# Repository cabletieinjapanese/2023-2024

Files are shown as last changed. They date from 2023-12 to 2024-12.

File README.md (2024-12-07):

repository for robocup bot, 2024 Singapore Robocup Open season

*updated 5 apr 2024*
## team, roles
loh hao yuan - elec, programming

lee yu zhe - mech, programming

cruz low, oliver ong - logistics, soldering

## final results
(5 apr 2024) 
due to a variety of factors (including misinterpretation of registration information, delays in robot production, lack of time for organiser to make adjustments), we were unable to participate in the 2024 Singapore Robocup Open.

throughout the past year, we've learnt a lot about the workings of a robocup bot, and we'll be back next year to finally prove our worth

we're currently working to finish up and polish our bot, such that we can run a few scrim games before starting anew with our bot for the 2024-2025 season.

## remarks
* everything here is half cooked spaghetti
    * we spent a lot of our time this year trying to figure things out, so a lot of stuff here is the result of trial and error
    * i guess our learning can be shown through the different versions, but theres many many areas which have a lot of potential for improvement
* version control
    * we didn't really use our github repository that much, which is a really bad practice
    * furthermore, one of our members has still not figured out how version control works, and consistently asks me to "help (him) push the code"  

## thanks
* [Sentinels Robotics](https://github.com/senrobo)
    * [@vincentcayadi](https://github.com/vincentcayadi) for his advice regarding the sport and life as a whole, his boundless enthusiasm, faith in our capabilities and good humour
    * [@shuanluck](https://github.com/shuanluck), [@DavidLow22](https://github.com/DavidLow22), and Tan Kian Wu for advice in all areas of robocup
* [Ducc Robotics](https://github.com/8076ducc)
    * [@neohaojun](https://github.com/neohaojun) for guidance and advice with regards to budgeting

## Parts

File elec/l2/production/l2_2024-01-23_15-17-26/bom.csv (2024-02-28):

Designator | Footprint | Quantity | Value | LCSC Part #
AWG1, AWG2 | 14 AWG | 2 | MountingHole
C1 | cap0603 | 1 | 10n
C2, C5 | EIA-7343-D | 2 | 220u
C3, C6 | cap0603 | 2 | C
C4 | cap0603 | 1 | 10u
D1_2, D1 | DIOM7959X265N | 2 | B340
H10, H11, H12, H13, H14, H3, H4, H5, H6, H7, H8, H9 | MountingHole_3.2mm_M3_Pad_Via | 12 | MountingHole_Pad
J1, J2 | L298N | 2 | Conn_01x06
J3 | PinSocket_1x04_P1.27mm_Vertical | 1 | Conn_01x04
J5 | PinSocket_1x08_P2.54mm_Vertical | 1 | Conn_01x08
L1, L2 | 0630 One Piece Inductor | 2 | 15uH
R1, R101, R3 | res0603 | 3 | 10K
R102 | res0603 | 1 | 1K
R2 | res0603 | 1 | 5K9
R4 | res0603 | 1 | 3K24
SW101 | SW_PUSH_SPST | 1 | SW_Push
U1, U3 | TI_SO-PowerPAD-8 | 2 | TPS5430DDA
U2 | MODULE_DEV-15583 | 1 | DEV-15583

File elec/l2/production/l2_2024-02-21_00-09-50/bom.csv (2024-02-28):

Designator | Footprint | Quantity | Value | LCSC Part #
C1 | cap0603 | 1 | 10n
C2, C5 | EIA-7343-D | 2 | 220u
C3, C6 | cap0603 | 2 | C
C4 | cap0603 | 1 | 10u
D1, D2 | 0603 | 2 | B340
H1, H10, H11, H12, H13, H14, H15, H16, H2, H3, H4, H5, H6, H7, H8, H9 | MountingHole_3.2mm_M3_Pad_Via | 16 | MountingHole_Pad
J1, J2 | L298N | 2 | Conn_01x13
J3 | PinHeader_1x04_P2.54mm_Vertical | 1 | Conn_01x04
J5 | PinSocket_1x08_P2.54mm_Vertical | 1 | Conn_01x08
L1, L2 | 0630 One Piece Inductor | 2 | 15uH
R1, R101, R3 | res0603 | 3 | 10K
R102 | res0603 | 1 | 1K
R2 | res0603 | 1 | 5K9
R4 | res0603 | 1 | 3K24
SW101 | SW_PUSH_SPST | 1 | SW_Push
U1, U3 | TI_SO-PowerPAD-8 | 2 | TPS5430DDA
U2 | MODULE_DEV-15583 | 1 | DEV-15583
batawg1, batawg2 | 14 AWG | 2 | +12V

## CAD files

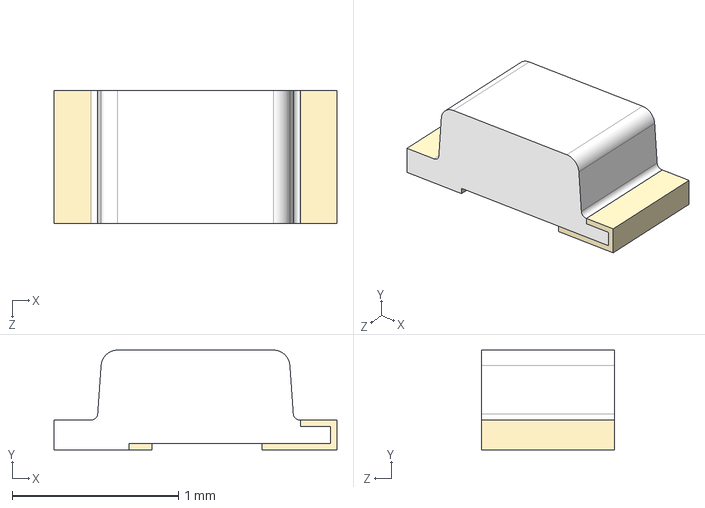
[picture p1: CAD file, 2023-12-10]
elec/2024l1/3dmodels/ALS-PT19.step
1.70 x 0.6 x 0.8 mm

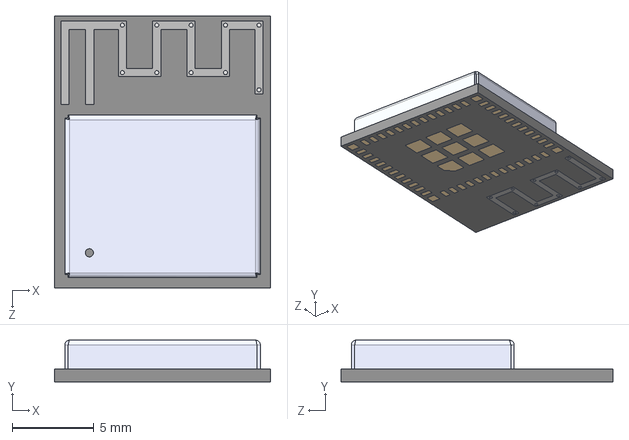
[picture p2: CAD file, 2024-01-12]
elec/l2/ESP32-C/ESP32-C3-MINI-1-N4.step
13.2 x 2.55 x 16.6 mm

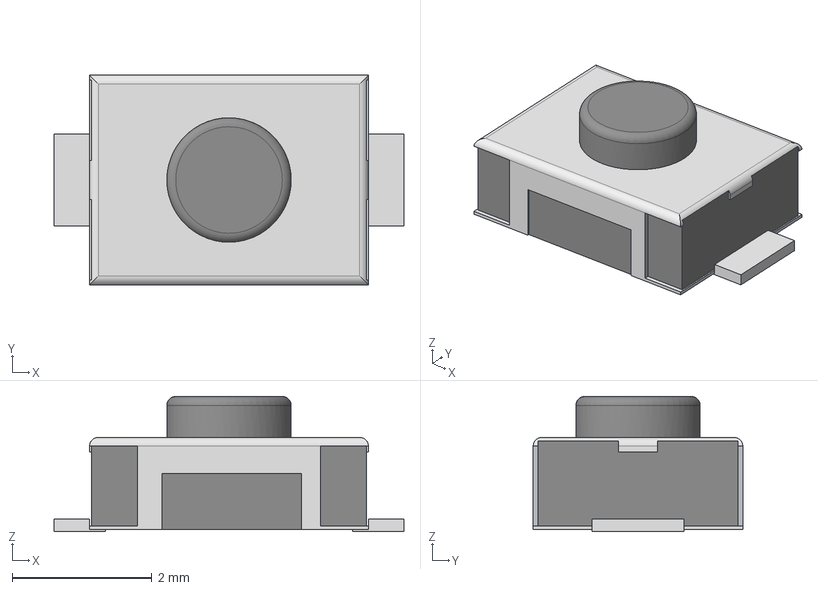
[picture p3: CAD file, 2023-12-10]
elec/2024l1/3dmodels/SW_PUSH_SPST.step
5.00 x 3.00 x 1.93 mm

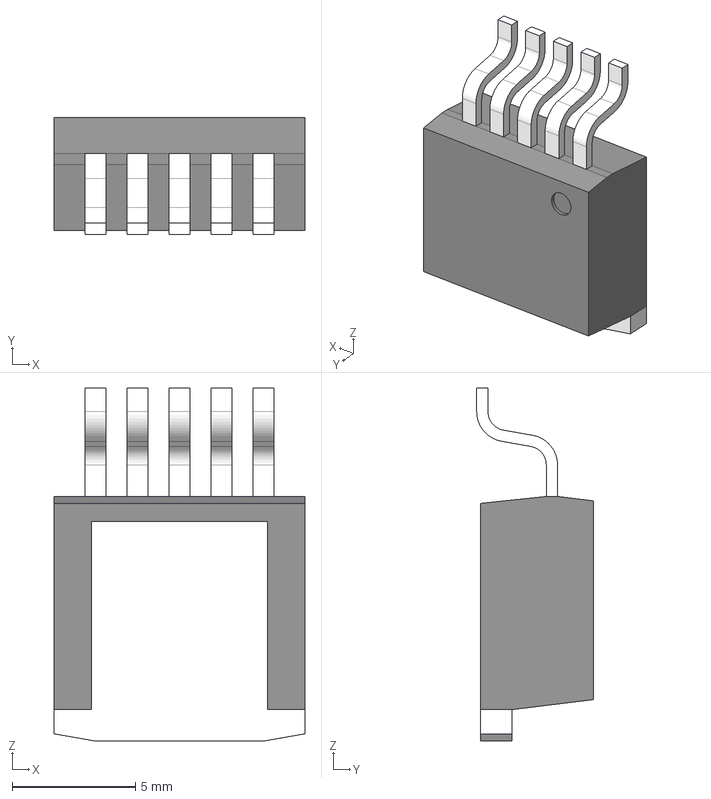
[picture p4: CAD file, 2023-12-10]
elec/2024l1/3dmodels/LM2587S.stp
10.2 x 4.72 x 14.3 mm
BODY_TS5B
HTSINK_TS5B
LEAD_TS5B x 5

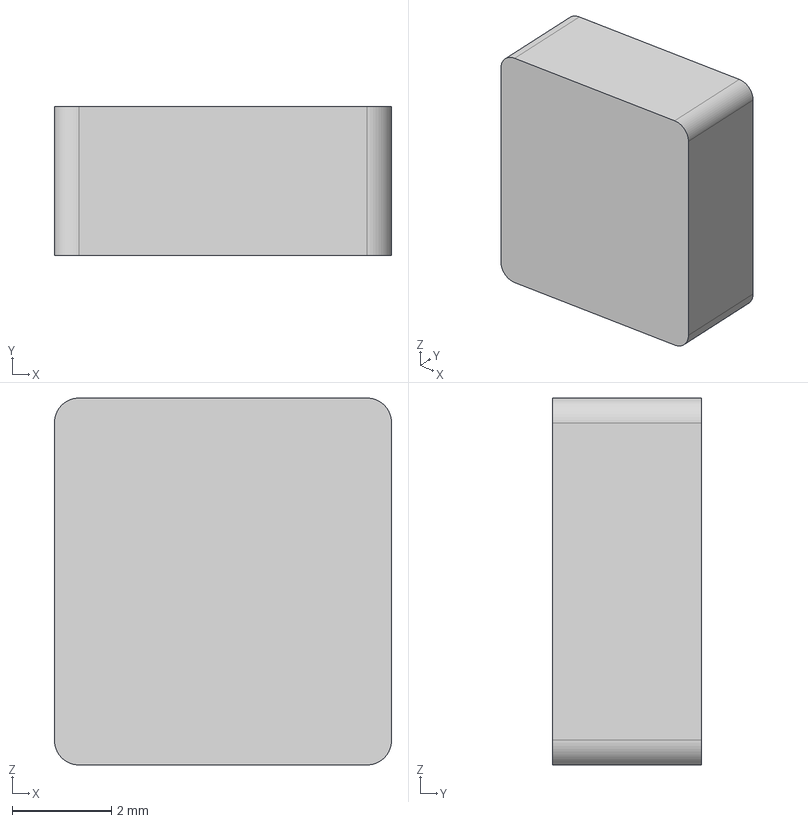
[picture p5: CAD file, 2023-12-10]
elec/2024l1/3dmodels/0603Inductor.step
6.80 x 3.00 x 7.40 mm

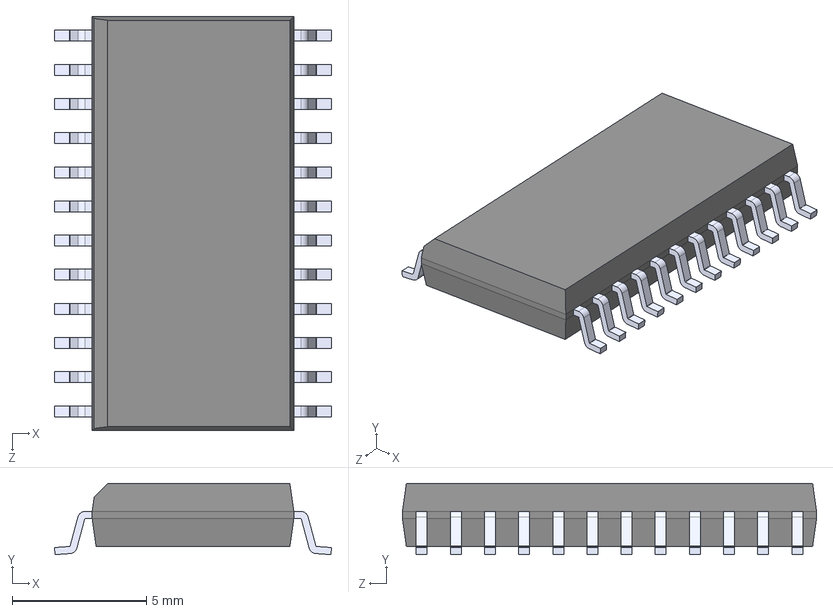
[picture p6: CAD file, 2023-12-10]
elec/2024l1/3dmodels/CD74HC4067M.step
10.3 x 2.65 x 15.4 mm

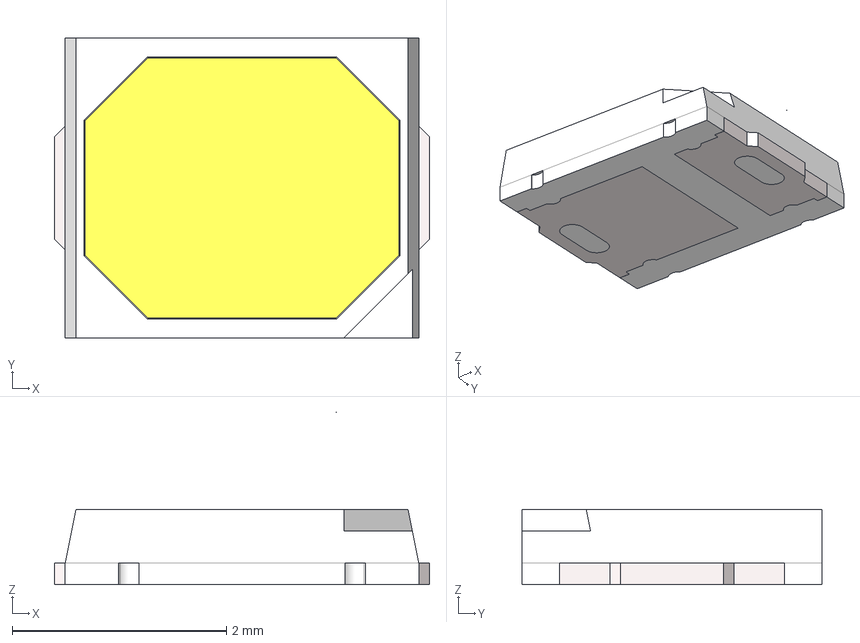
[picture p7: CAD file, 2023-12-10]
elec/2024l1/3dmodels/led2835.stp
3.50 x 2.80 x 1.61 mm

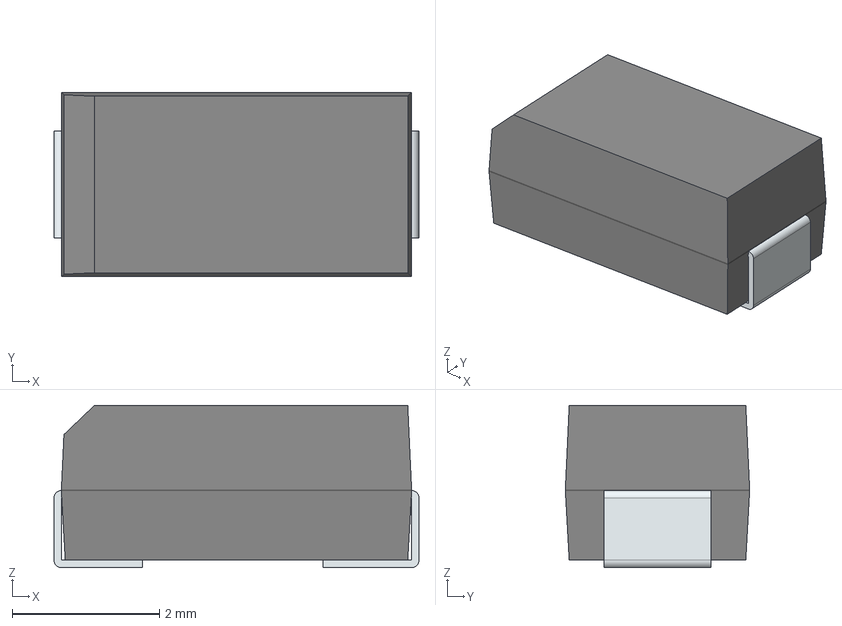
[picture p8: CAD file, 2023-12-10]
elec/2024l1/3dmodels/SS5X.stp
4.95 x 2.50 x 2.20 mm
FilletPin1
FilletPin2

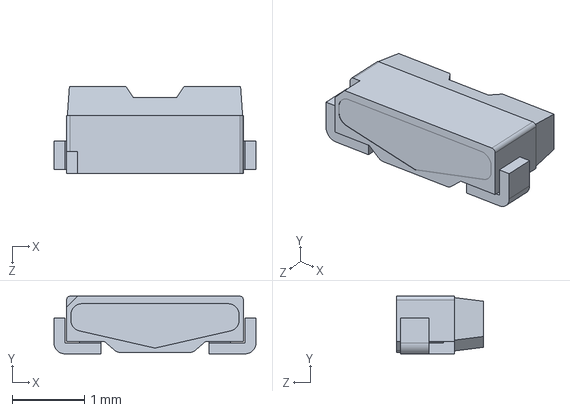
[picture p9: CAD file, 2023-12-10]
elec/2024l1/3dmodels/CSL04.step
2.80 x 0.8 x 1.20 mm

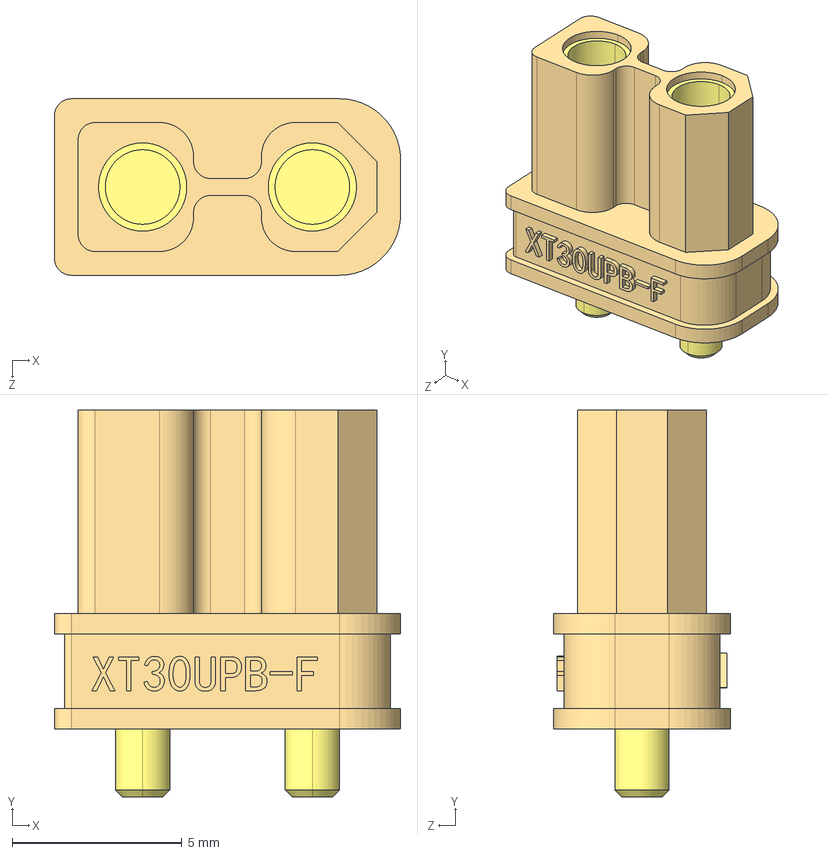
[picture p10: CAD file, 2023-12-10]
elec/2024l1/3dmodels/XT30UPB-F.step
10.2 x 11.4 x 5.20 mm

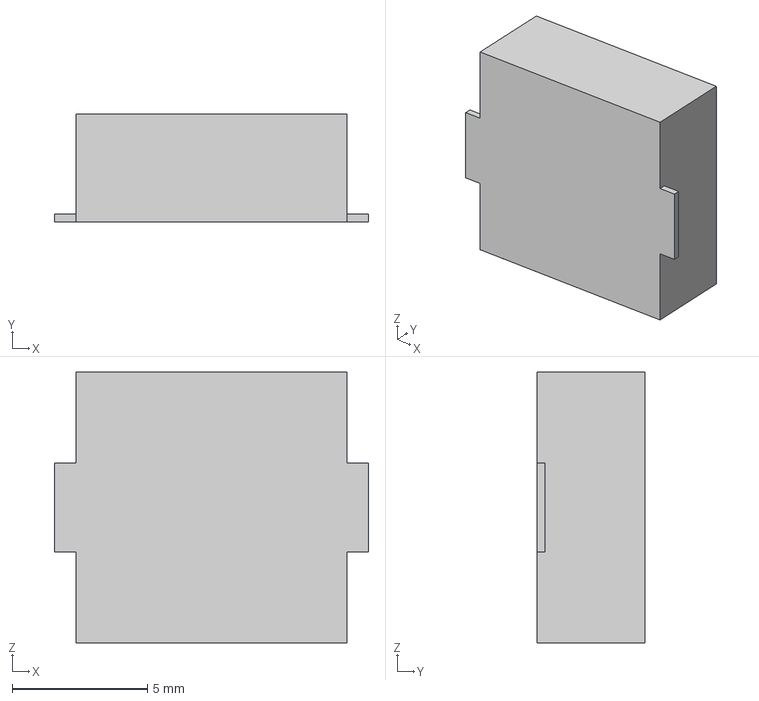
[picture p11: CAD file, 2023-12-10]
elec/2024l1/3dmodels/1040 inductor v1.step
11.6 x 4.00 x 10.0 mm

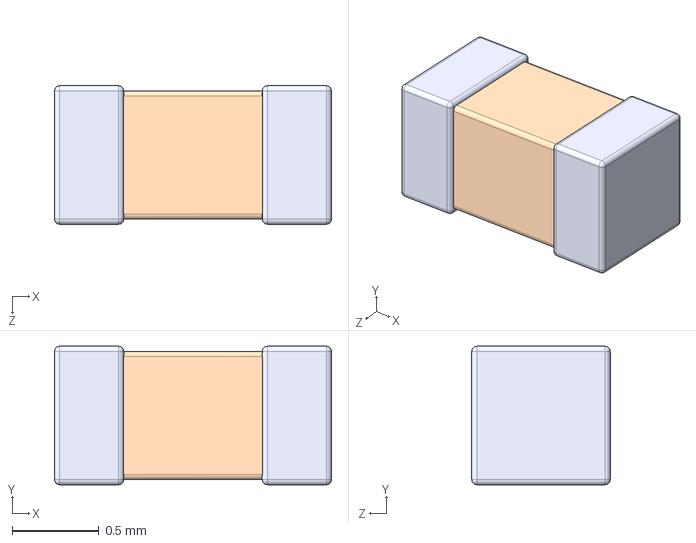
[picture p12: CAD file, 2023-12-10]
elec/2024l1/3dmodels/C0603.step
1.60 x 0.8 x 0.8 mm

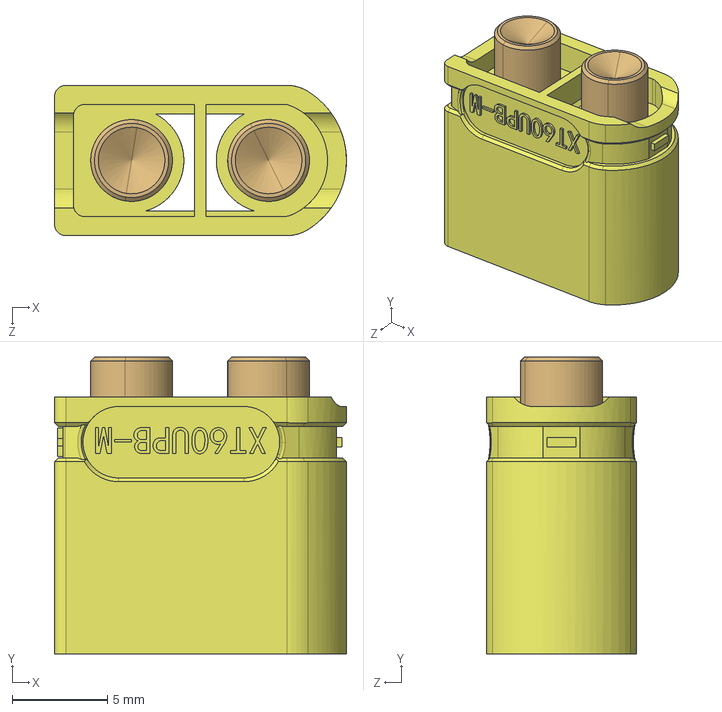
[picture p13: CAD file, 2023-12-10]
elec/2024l1/3dmodels/XT60UPB-M.step
15.3 x 15.6 x 7.90 mm
XT60UPB-M呿璃-UL
60UPB-MTJ x 2

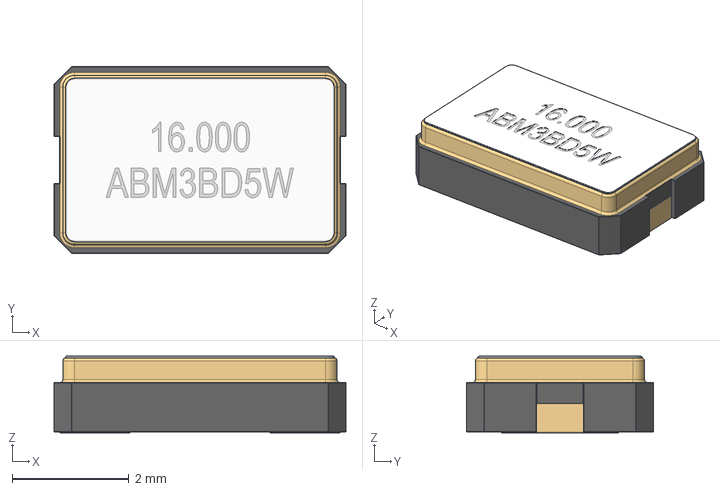
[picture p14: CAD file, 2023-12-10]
elec/2024l1/3dmodels/Crystal.step
5.00 x 3.20 x 1.31 mm

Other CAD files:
elec/2024l1/3dmodels/led0603.step
elec/2024l1/3dmodels/SS12D00G3.stp
elec/2024l1/3dmodels/IRLML6344TRPBF.stp
elec/2024l1/3dmodels/LED 5mm, Green, Thru-hole, Right Angle PCB 2.stp
elec/2024l1/3dmodels/3362W.stp
elec/2024l1/3dmodels/LED3528.step
elec/2024l1/3dmodels/R0603.step
elec/2024l1/3dmodels/STP75NF75.step
elec/archives/original l1/3dmodels/0603Inductor.step
elec/archives/original l1/3dmodels/1040Inductor.step
elec/archives/original l1/3dmodels/3362W.stp
elec/archives/original l1/3dmodels/ALS-PT19.step
elec/archives/original l1/3dmodels/C0603.step
elec/archives/original l1/3dmodels/Crystal.step
elec/archives/original l1/3dmodels/LED3528.step
elec/archives/original l1/3dmodels/LM2587S.stp
elec/archives/original l1/3dmodels/R0603.step
elec/archives/original l1/3dmodels/SS12D00G3.stp
elec/archives/original l1/3dmodels/SS5X.stp
elec/archives/original l1/3dmodels/STP75NF75.step
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

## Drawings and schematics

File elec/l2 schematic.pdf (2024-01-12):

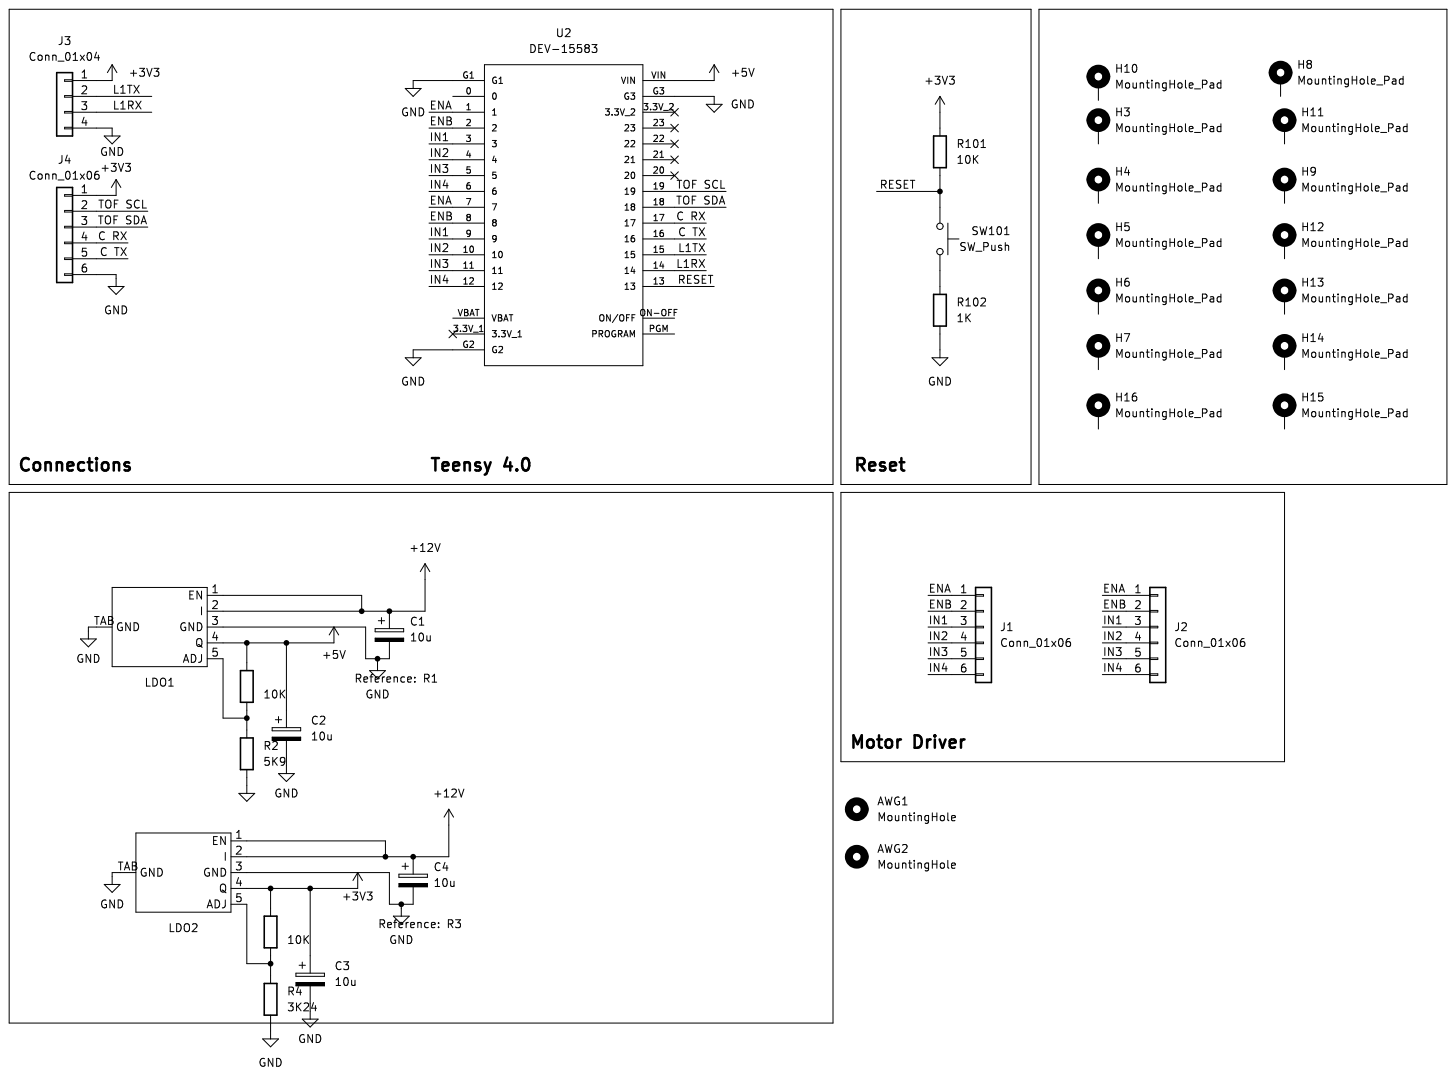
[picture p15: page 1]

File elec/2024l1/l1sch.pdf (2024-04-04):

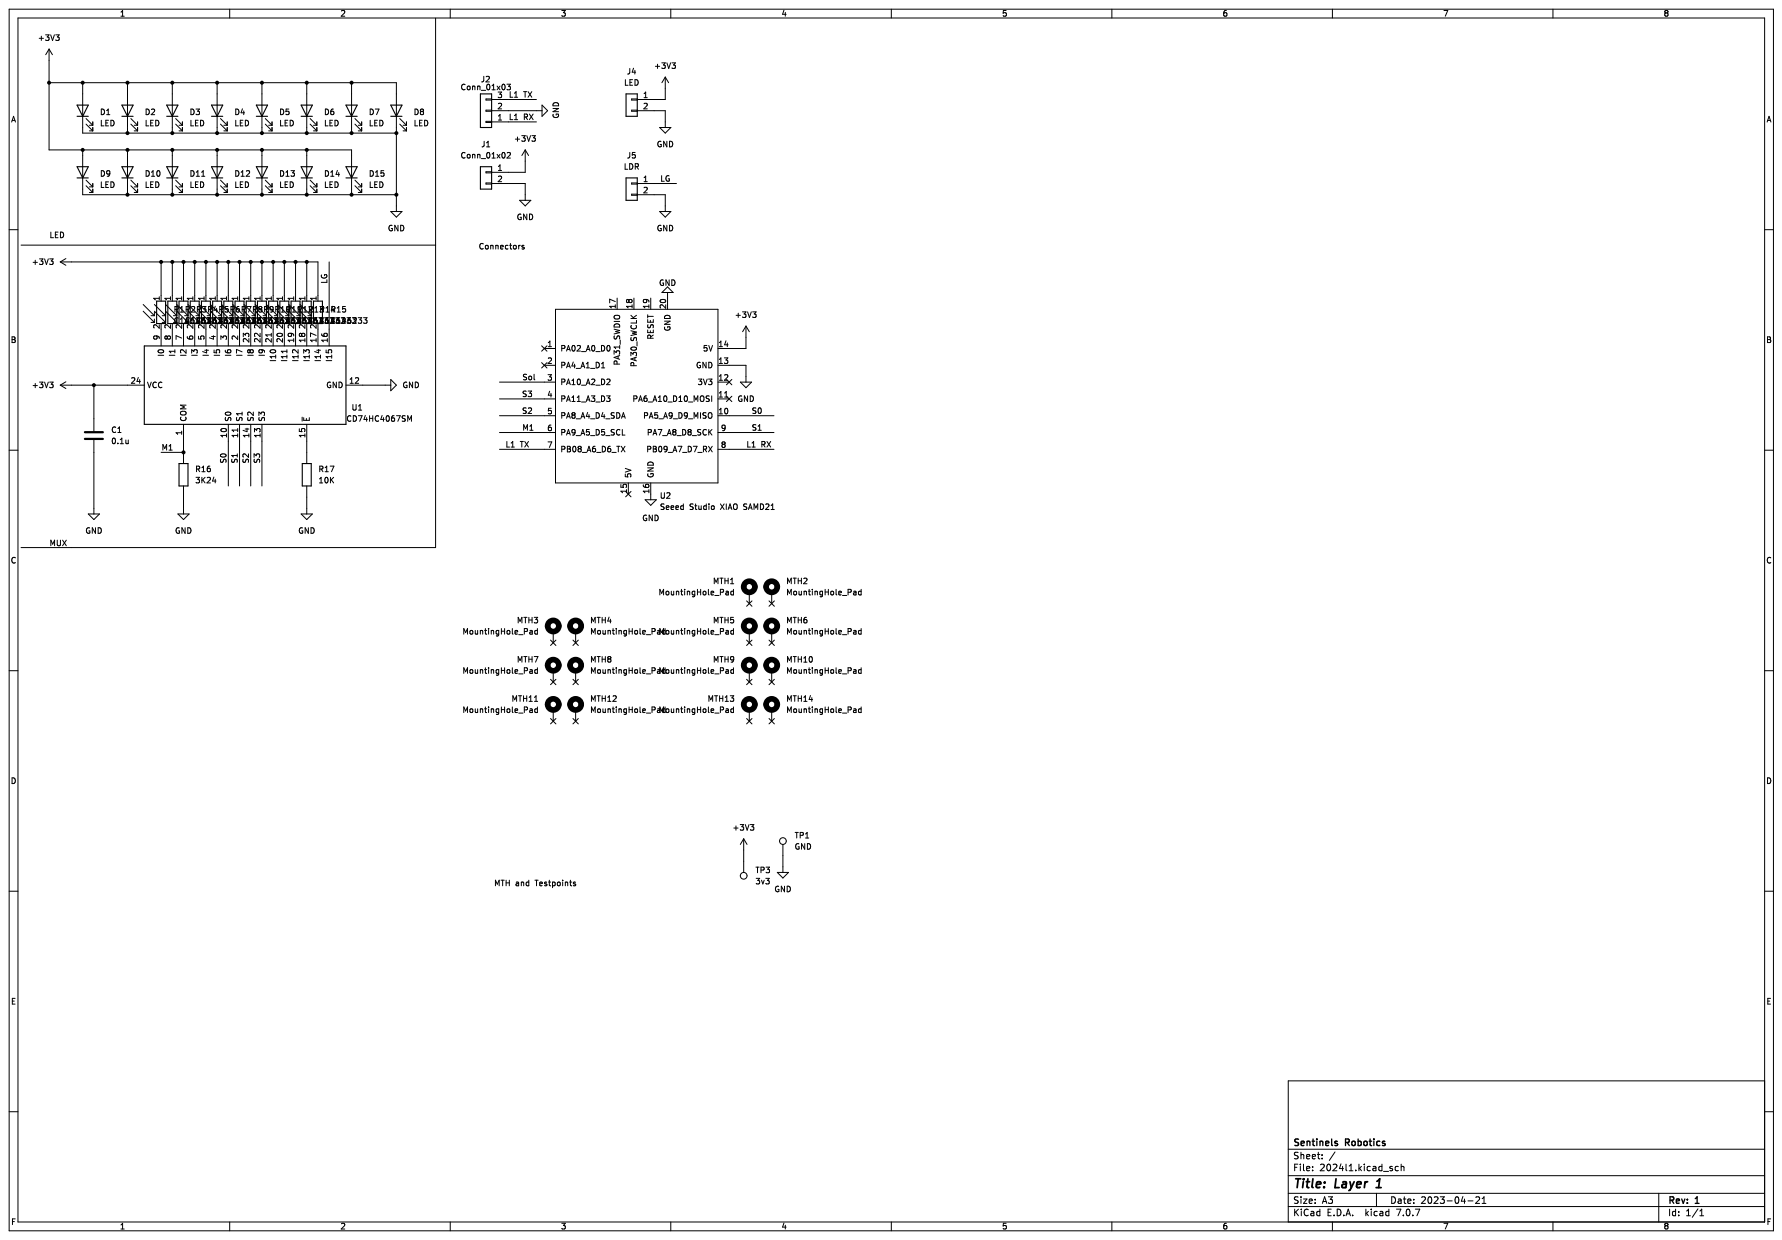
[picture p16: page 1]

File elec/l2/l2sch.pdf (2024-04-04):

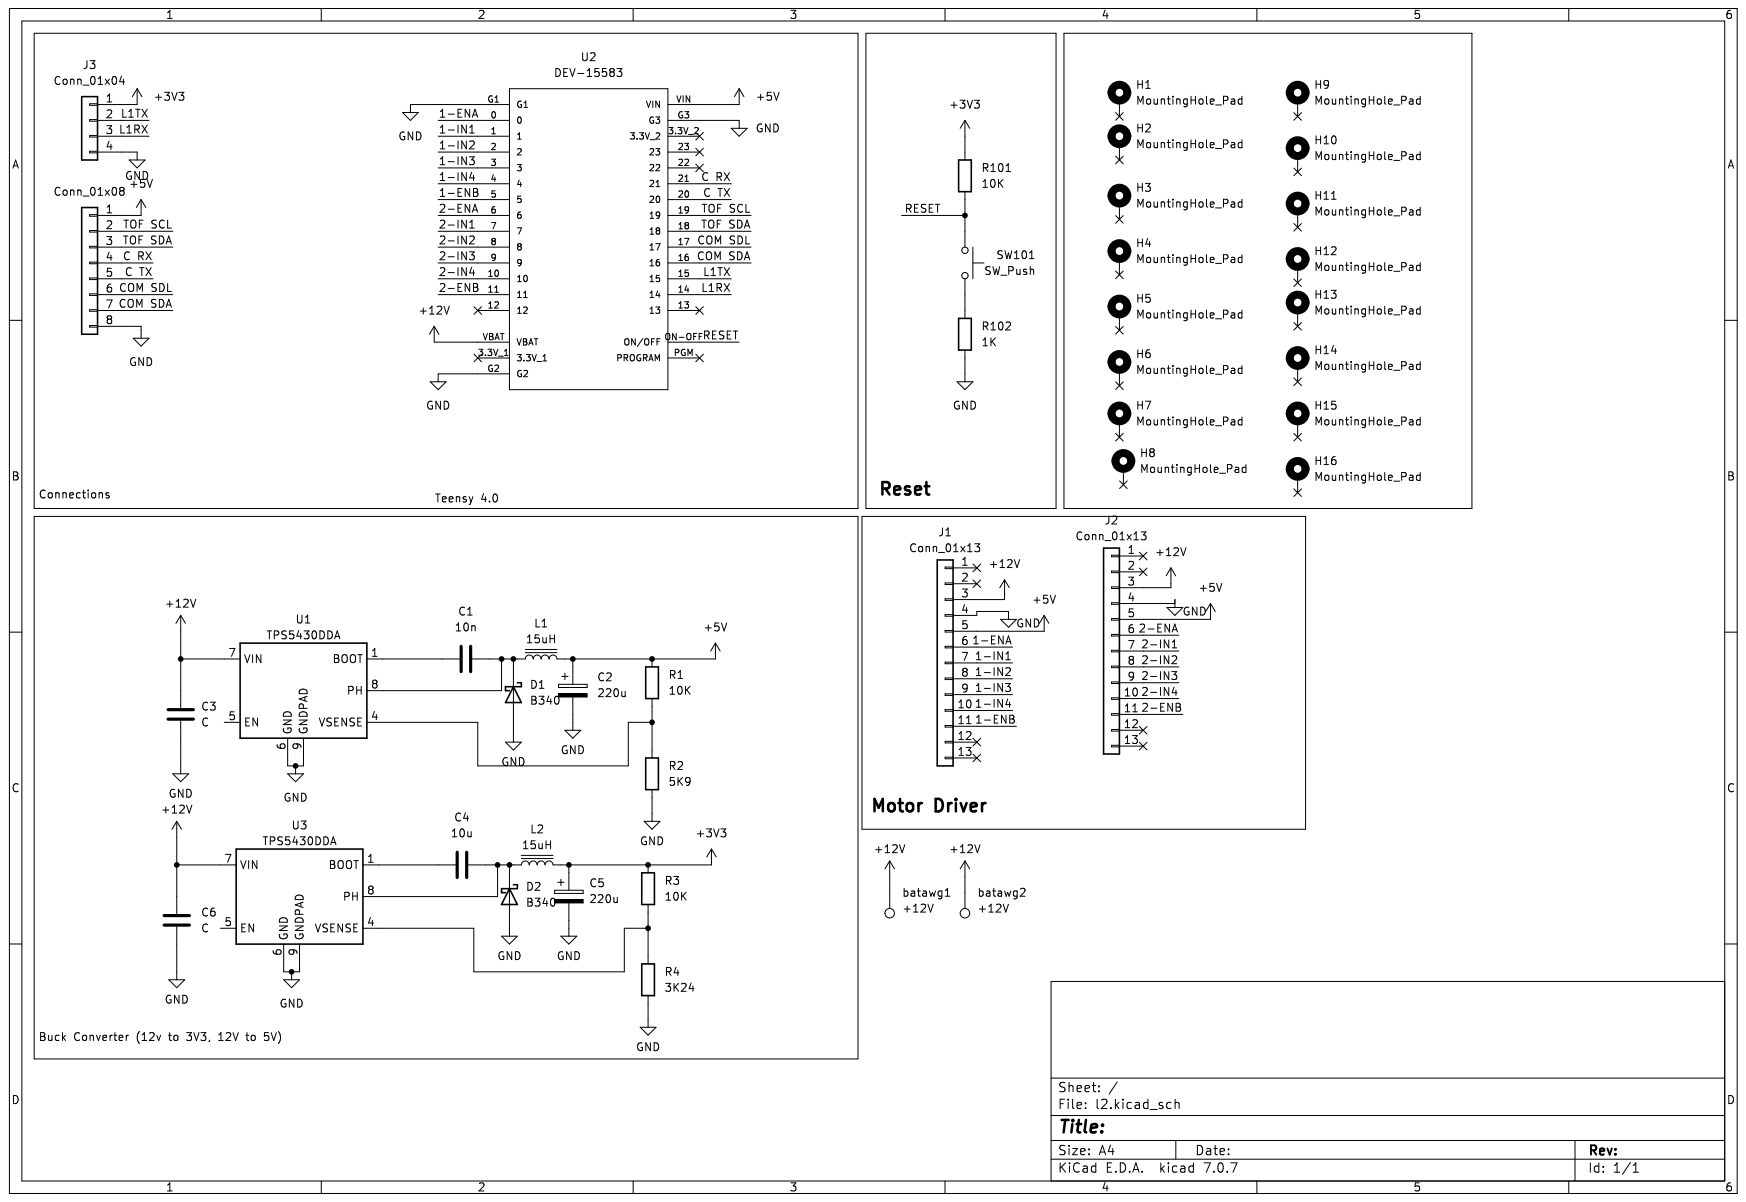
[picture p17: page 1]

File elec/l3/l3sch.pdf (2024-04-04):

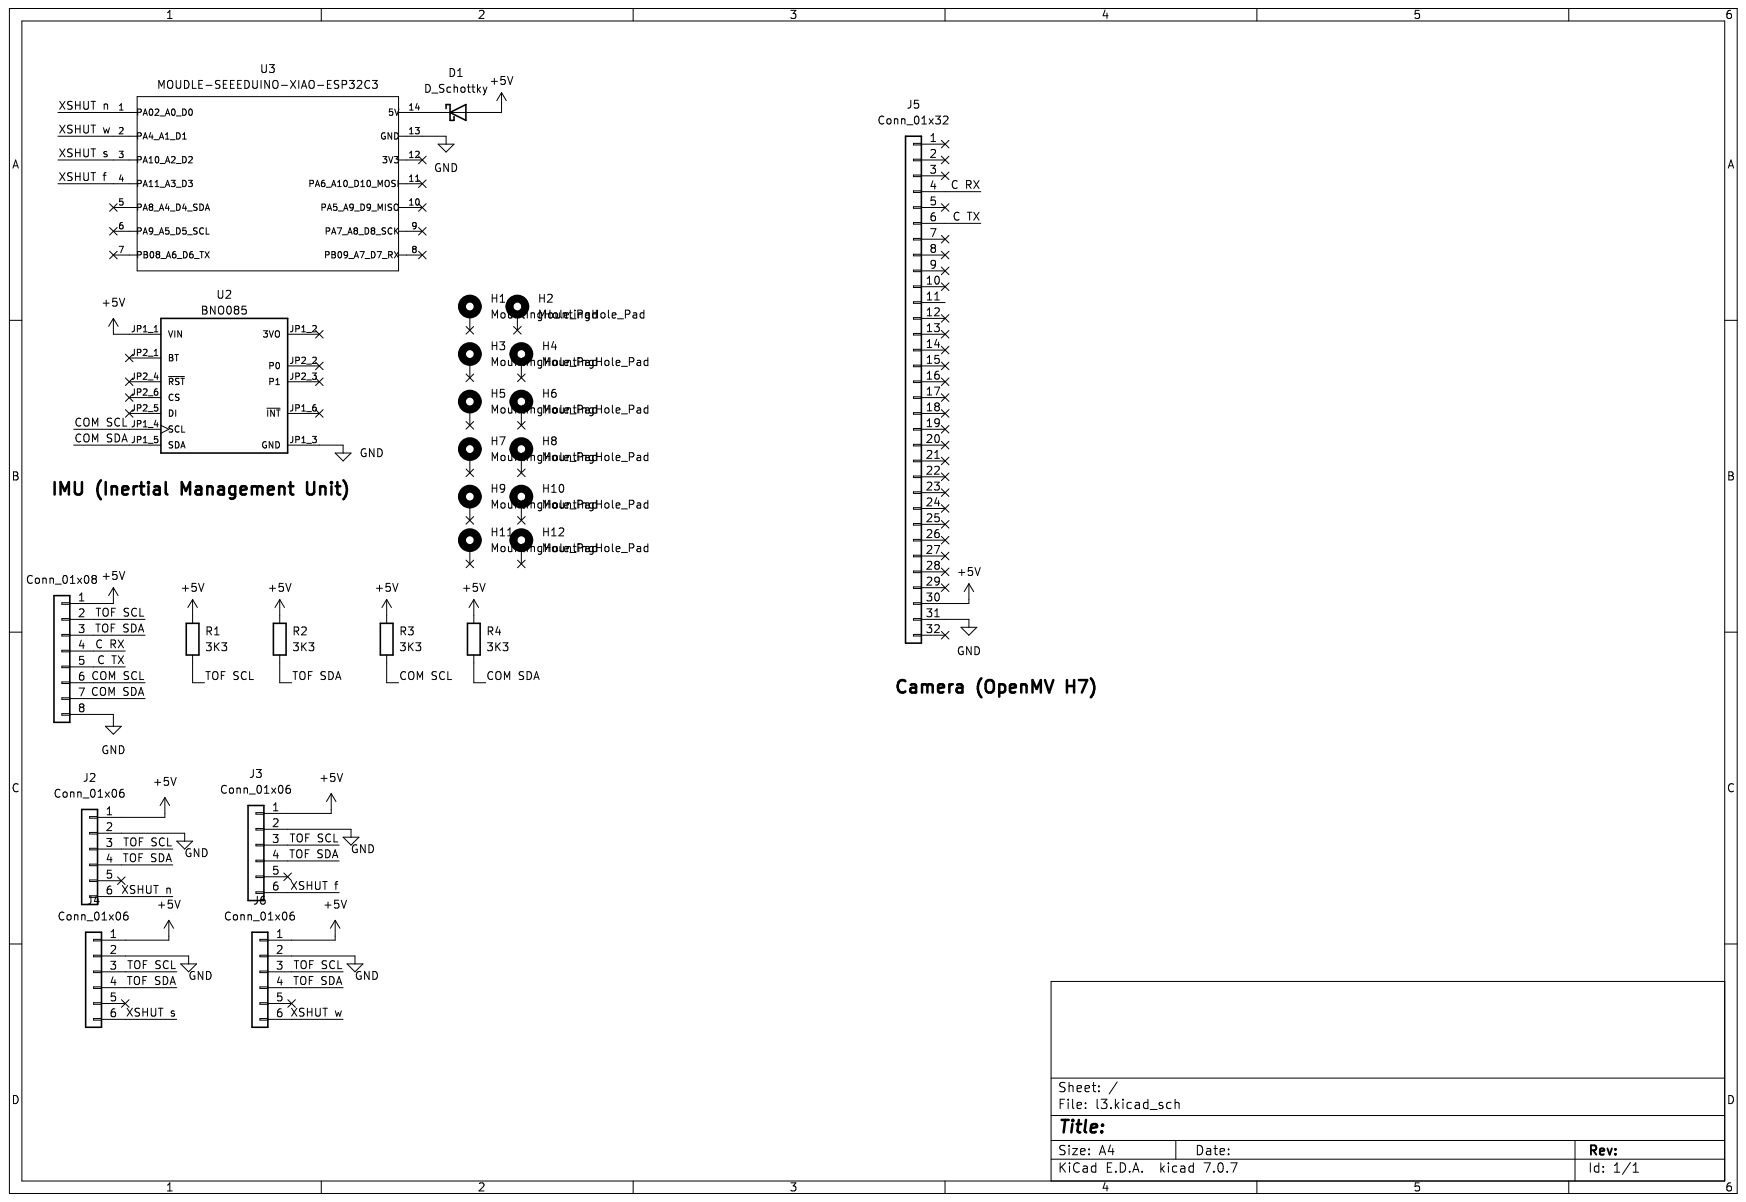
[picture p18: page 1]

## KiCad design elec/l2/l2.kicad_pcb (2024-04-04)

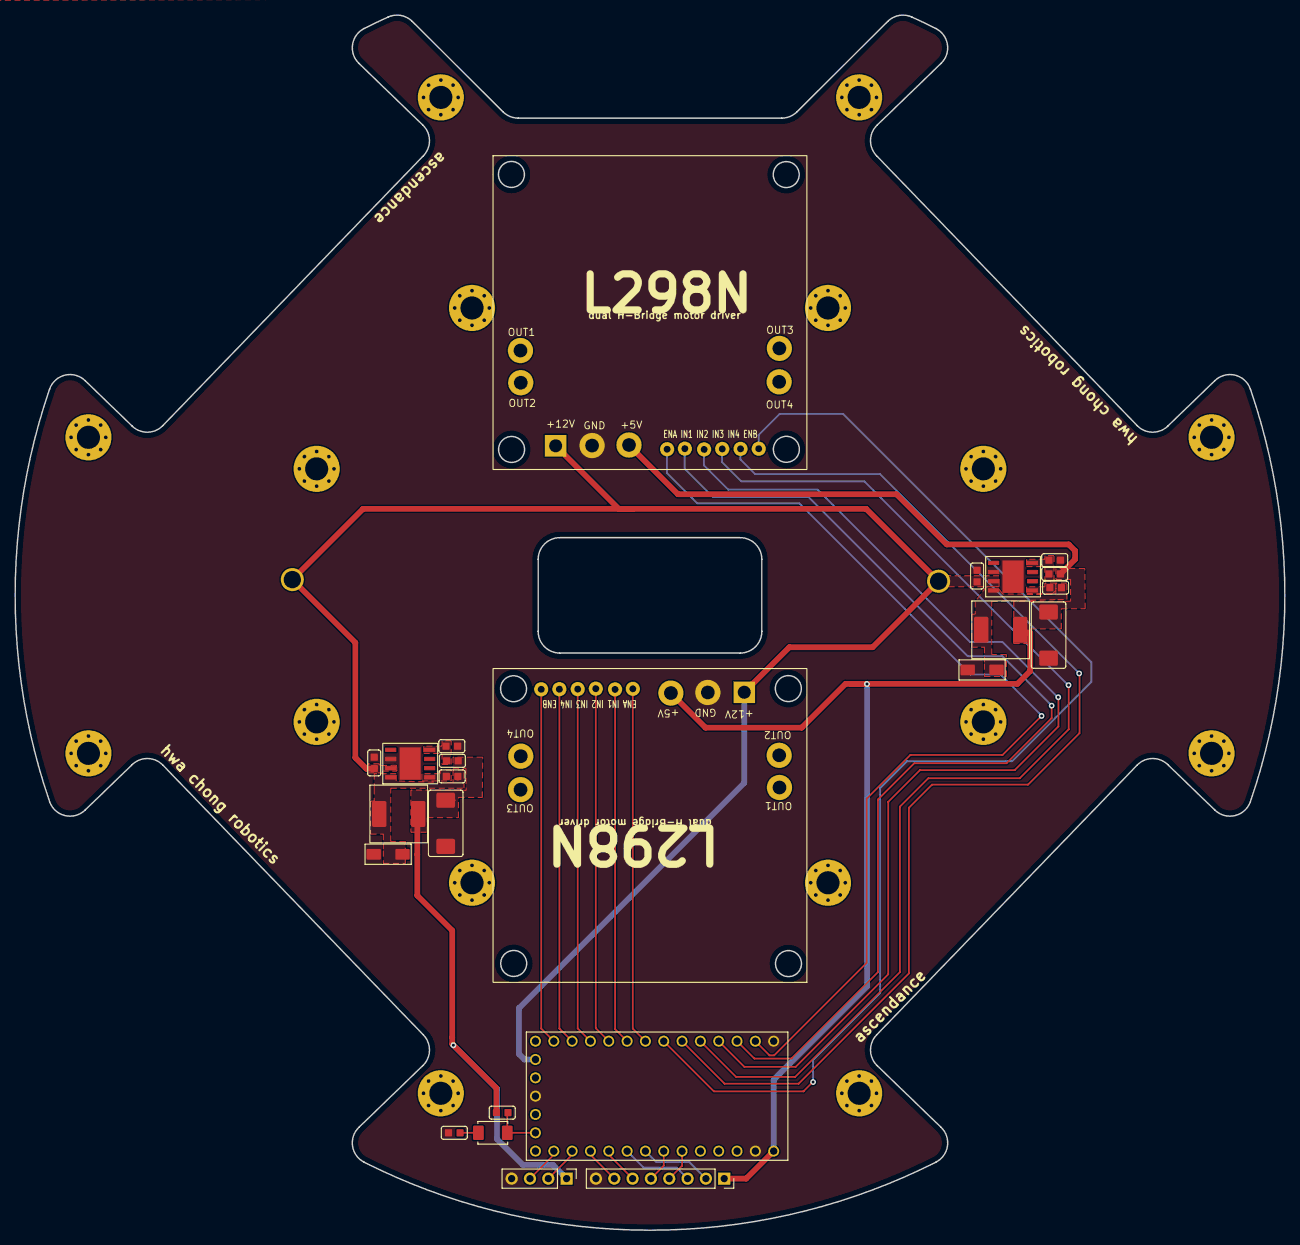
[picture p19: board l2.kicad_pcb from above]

Board: 2 copper layers, 176.0 x 168.4 mm, 42 parts (0 on the bottom side), 32 nets.

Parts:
C1: 10n; cap0603
C2, C5: 220u; EIA-7343-D
C3, C6: C; cap0603
C4: 10u; cap0603
D1, D2: B340; DIOM5025X220N
H1, H2, H3, H4, H5, H6, H7, H8, H9, H10, H11, H12, H13, H14, H15, H16: MountingHole_Pad; MountingHole_3.2mm_M3_Pad_Via
J1, J2: Conn_01x13; L298N
J3: Conn_01x04; PinHeader_1x04_P2.54mm_Vertical
J5: Conn_01x08; PinSocket_1x08_P2.54mm_Vertical
L1, L2: 15uH; 0630 One Piece Inductor
R1, R3, R101: 10K; res0603
R2: 5K9; res0603
R4: 3K24; res0603
R102: 1K; res0603
SW101: SW_Push; SW_PUSH_SPST
U1, U3: TPS5430DDA; TI_SO-PowerPAD-8
U2: DEV-15583; MODULE_DEV-15583
batawg1, batawg2: +12V; 14 AWG

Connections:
+3V3: C5.1, J3.1, L2.2, R3.1, R101.1
+5V: C2.1, J1.5, J2.5, J5.1, L1.2, R1.1, U2.VIN
+12V: C3.1, C6.1, J1.3, J2.3, U1.7 (VIN), U2.VBAT, U3.7 (VIN), batawg1.1, batawg2.1
/1-ENA: J1.6, U2.0
/1-ENB: J1.11, U2.5
/1-IN1: J1.7, U2.1
/1-IN2: J1.8, U2.2
/1-IN3: J1.9, U2.3
/1-IN4: J1.10, U2.4
/2-ENA: J2.6, U2.6
/2-ENB: J2.11, U2.11
/2-IN1: J2.7, U2.7
/2-IN2: J2.8, U2.8
/2-IN3: J2.9, U2.9
/2-IN4: J2.10, U2.10
/C RX: J5.4, U2.21
/C TX: J5.5, U2.20
/COM SDA: J5.7, U2.16
/COM SDL: J5.6, U2.17
/L1RX: J3.3, U2.14
/L1TX: J3.2, U2.15
/RESET: R101.2, SW101.2, U2.ON-OFF (ON/OFF)
/TOF SCL: J5.2, U2.19
/TOF SDA: J5.3, U2.18
GND: C2.2, C3.2, C5.2, C6.2, D1.2 (A), D2.2 (A), J1.4, J2.4, J3.4, J5.8, R2.2, R4.2, R102.2, U1.6 (GND), U1.9 (GNDPAD), U2.G1, U2.G2, U2.G3, U3.6 (GND), U3.9 (GNDPAD)
unnamed: C1.2, D1.1 (K), L1.1, U1.8 (PH)
unnamed: C4.1, D2.1 (K), L2.1, U3.8 (PH)
unnamed: R102.1, SW101.1
unnamed: C1.1, U1.1 (BOOT)
unnamed: R1.2, R2.1, U1.4 (VSENSE)
unnamed: C4.2, U3.1 (BOOT)
unnamed: R3.2, R4.1, U3.4 (VSENSE)

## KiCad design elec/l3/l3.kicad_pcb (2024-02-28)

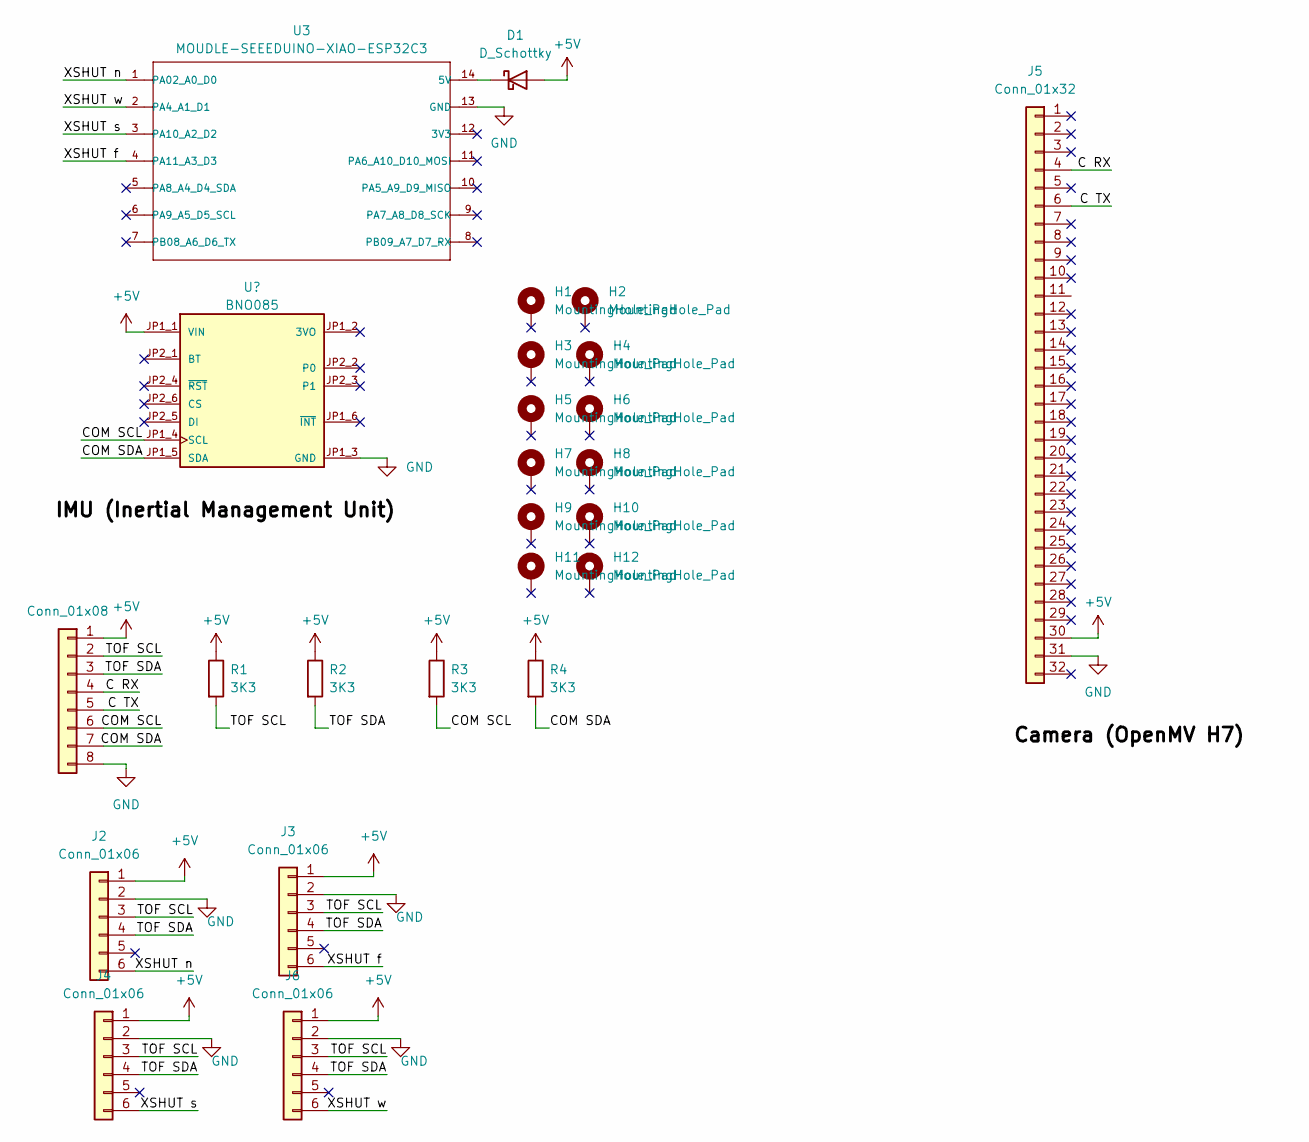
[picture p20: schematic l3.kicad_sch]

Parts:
D1: D_Schottky; D_0603_1608Metric_Pad1.05x0.95mm_HandSolder
H1, H2, H3, H4, H5, H6, H7, H8, H9, H10, H11, H12: MountingHole_Pad; MountingHole_3mm_Pad_Via
J1: Conn_01x08; PinSocket_1x08_P2.54mm_Vertical
J2, J3, J4, J6: Conn_01x06; PinSocket_1x06_P2.54mm_Vertical
J5: Conn_01x32; OpenMV_RT
R1, R2, R3, R4: 3K3; res0603
U2: BNO085; bno085; PARTREV 2021-03-16
U3: MOUDLE-SEEEDUINO-XIAO-ESP32C3; Seeeduino XIAO SAMD 21 TFT

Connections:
+5V: D1.2 (A), J1.1, J2.1, J3.1, J4.1, J5.30, J6.1, R1.1, R2.1, R3.1, R4.1, U2.JP1_1 (VIN)
/C RX: J1.4, J5.4
/C TX: J1.5, J5.6
/COM SCL: J1.6, R3.2, U2.JP1_4 (SCL)
/COM SDA: J1.7, R4.2, U2.JP1_5 (SDA)
/TOF SCL: J1.2, J2.3, J3.3, J4.3, J6.3, R1.2
/TOF SDA: J1.3, J2.4, J3.4, J4.4, J6.4, R2.2
/XSHUT f: J3.6, U3.4 (PA11_A3_D3)
/XSHUT n: J2.6, U3.1 (PA02_A0_D0)
/XSHUT s: J4.6, U3.3 (PA10_A2_D2)
/XSHUT w: J6.6, U3.2 (PA4_A1_D1)
GND: J1.8, J2.2, J3.2, J4.2, J5.31, J6.2, U2.JP1_3 (GND), U3.13 (GND)
unnamed: D1.1 (K), U3.14 (5V)

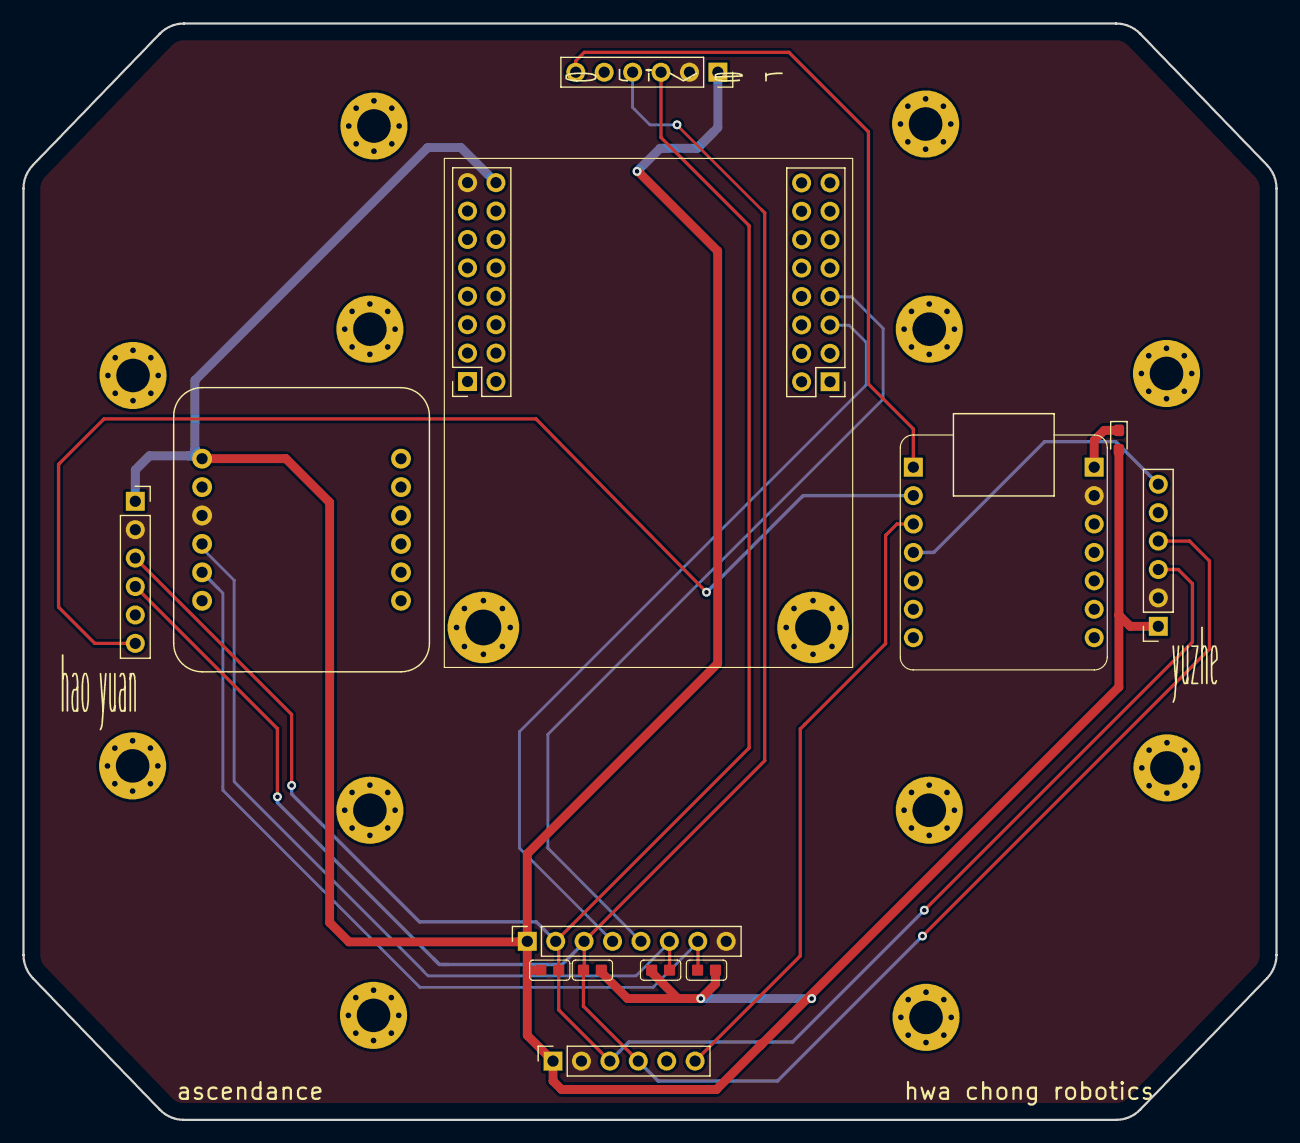
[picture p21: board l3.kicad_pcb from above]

Board: 2 copper layers, 112.0 x 98.0 mm, 25 parts (0 on the bottom side), 13 nets.

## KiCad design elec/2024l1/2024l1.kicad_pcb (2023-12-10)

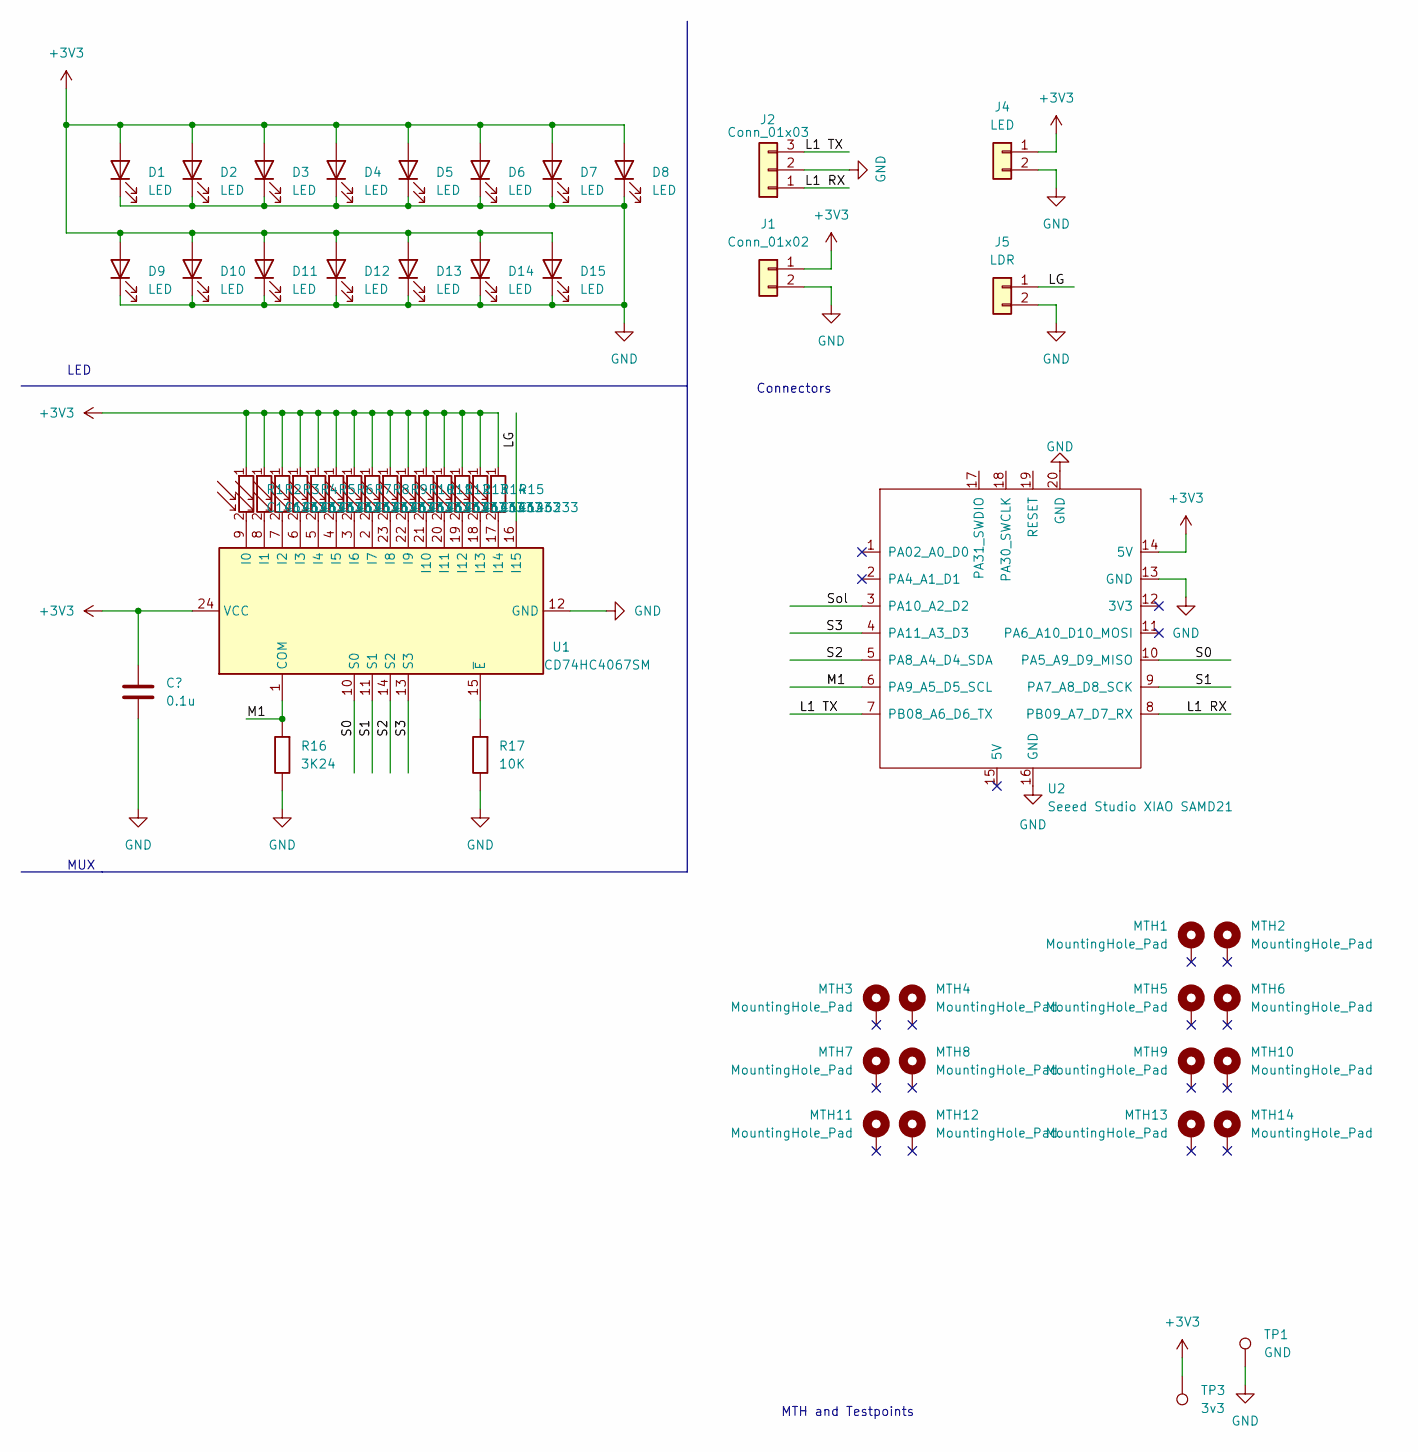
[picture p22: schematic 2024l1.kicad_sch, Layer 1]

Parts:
C1: 0.1u; cap0603; LCSC C5463924
D1, D2, D3, D4, D5, D6, D7, D8, D9, D10, D11, D12, D13, D14, D15: LED; led2835; LCSC C7423442
J1: Conn_01x02; JST_XH_B2B-XH-A_1x02_P2.50mm_Vertical
J2: Conn_01x03; JST_XH_B3B-XH-A_1x03_P2.50mm_Vertical; LCSC C144394
J4: LED; PinSocket_1x02_P2.54mm_Vertical
J5: LDR; PinSocket_1x02_P2.54mm_Vertical
MTH1, MTH2, MTH3, MTH4, MTH5, MTH6, MTH7, MTH8, MTH9, MTH10, MTH11, MTH12, MTH13, MTH14: MountingHole_Pad; MountingHole_3.2mm_M3_Pad_Via
R1, R2, R3, R4, R5, R6, R7, R8, R9, R10, R11, R12, R13, R14, R15: C146233; ALS-PT19 (Top Side); LCSC C146233
R16: 3K24; res0603; LCSC C22994
R17: 10K; res0603; LCSC C25804
TP1: GND; 14 AWG
TP3: 3v3; 14 AWG
U1: CD74HC4067SM; CD74HC4067M; LCSC C1545936
U2: Seeed Studio XIAO SAMD21; Seeeduino XIAO SAMD 21 TFT

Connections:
+3V3: C1.1, D1.2 (A), D2.2 (A), D3.2 (A), D4.2 (A), D5.2 (A), D6.2 (A), D7.2 (A), D8.2 (A), D9.2 (A), D10.2 (A), D11.2 (A), D12.2 (A), D13.2 (A), D14.2 (A), D15.2 (A), J1.1, J4.1, R1.1, R2.1, R3.1, R4.1, R5.1, R6.1, R7.1, R8.1, R9.1, R10.1, R11.1, R12.1, R13.1, R14.1, R15.1, TP3.1, U1.24 (VCC), U2.14 (5V)
/L1 RX: J2.1, U2.8 (PB09_A7_D7_RX)
/L1 TX: J2.3, U2.7 (PB08_A6_D6_TX)
/LG: J5.1, U1.16 (I15)
/M1: R16.2, U1.1 (COM), U2.6 (PA9_A5_D5_SCL)
/S0: U1.10 (S0), U2.10 (PA5_A9_D9_MISO)
/S1: U1.11 (S1), U2.9 (PA7_A8_D8_SCK)
/S2: U1.14 (S2), U2.5 (PA8_A4_D4_SDA)
/S3: U1.13 (S3), U2.4 (PA11_A3_D3)
/Sol: U2.3 (PA10_A2_D2)
GND: C1.2, D1.1 (K), D2.1 (K), D3.1 (K), D4.1 (K), D5.1 (K), D6.1 (K), D7.1 (K), D8.1 (K), D9.1 (K), D10.1 (K), D11.1 (K), D12.1 (K), D13.1 (K), D14.1 (K), D15.1 (K), J1.2, J2.2, J4.2, J5.2, R16.1, R17.1, TP1.1, U1.12 (GND), U2.13 (GND), U2.16 (GND), U2.20 (GND)
unnamed: R1.2, U1.9 (I0)
unnamed: R2.2, U1.8 (I1)
unnamed: R3.2, U1.7 (I2)
unnamed: R4.2, U1.6 (I3)
unnamed: R5.2, U1.5 (I4)
unnamed: R6.2, U1.4 (I5)
unnamed: R7.2, U1.3 (I6)
unnamed: R8.2, U1.2 (I7)
unnamed: R9.2, U1.23 (I8)
unnamed: R10.2, U1.22 (I9)
unnamed: R11.2, U1.21 (I10)
unnamed: R12.2, U1.20 (I11)
unnamed: R13.2, U1.19 (I12)
unnamed: R14.2, U1.18 (I13)
unnamed: R15.2, U1.17 (I14)
unnamed: R17.2, U1.15 (~E)

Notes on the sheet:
MUX
MTH and Testpoints
LED
Connectors

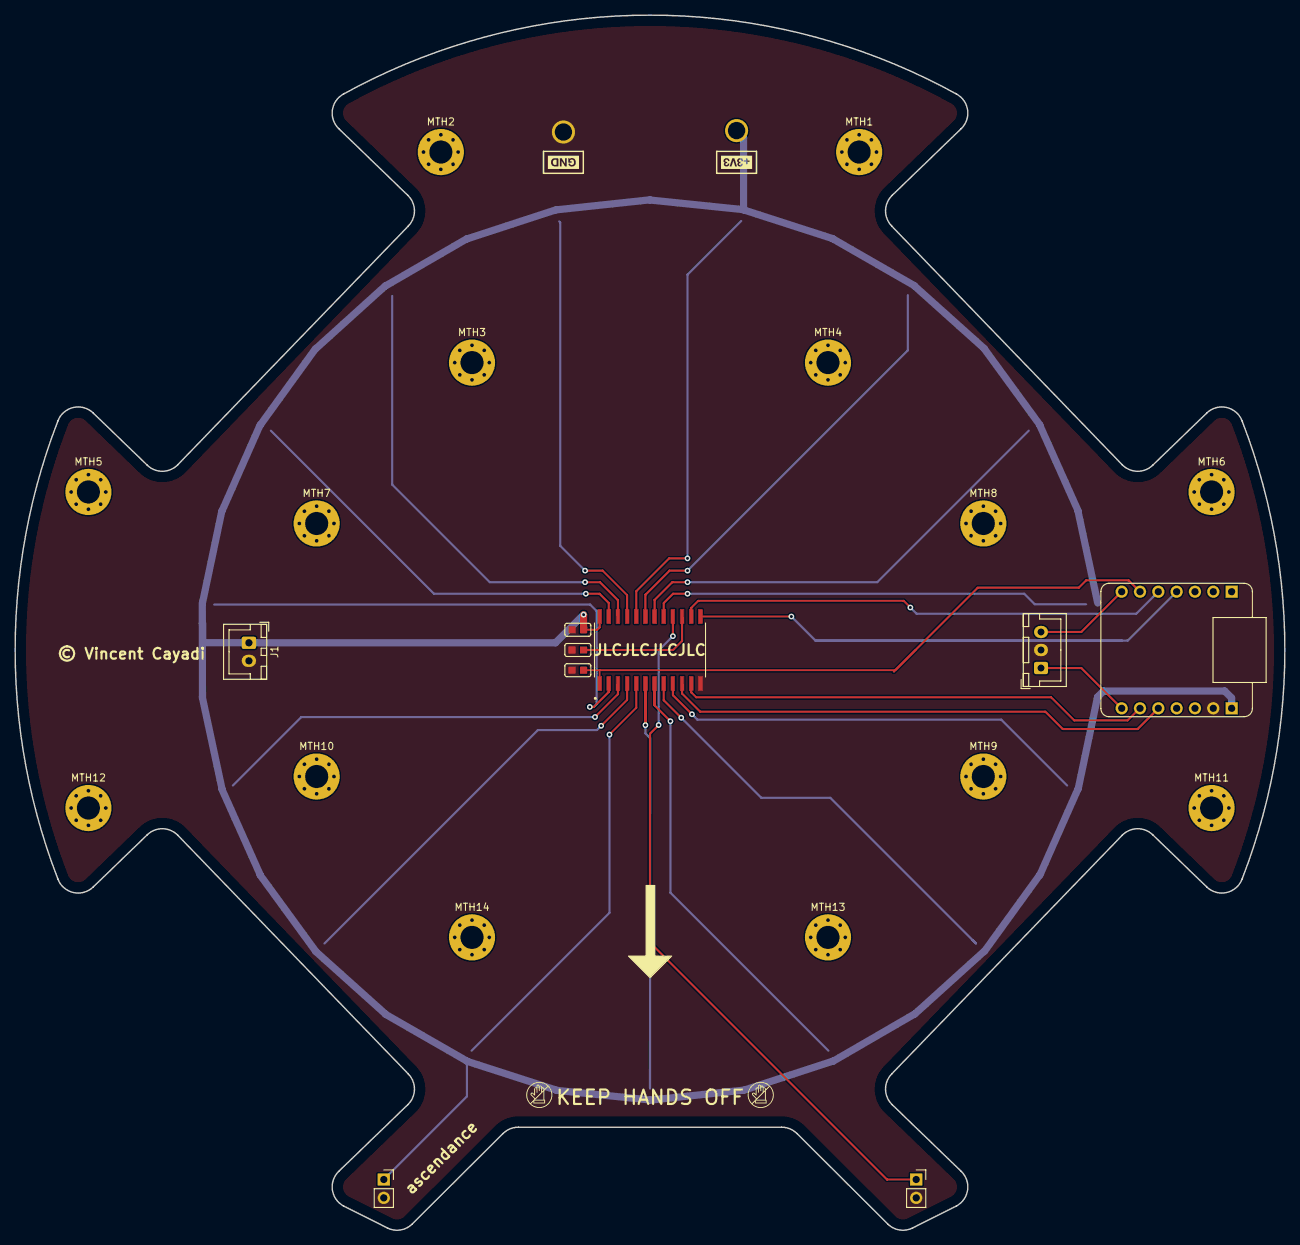
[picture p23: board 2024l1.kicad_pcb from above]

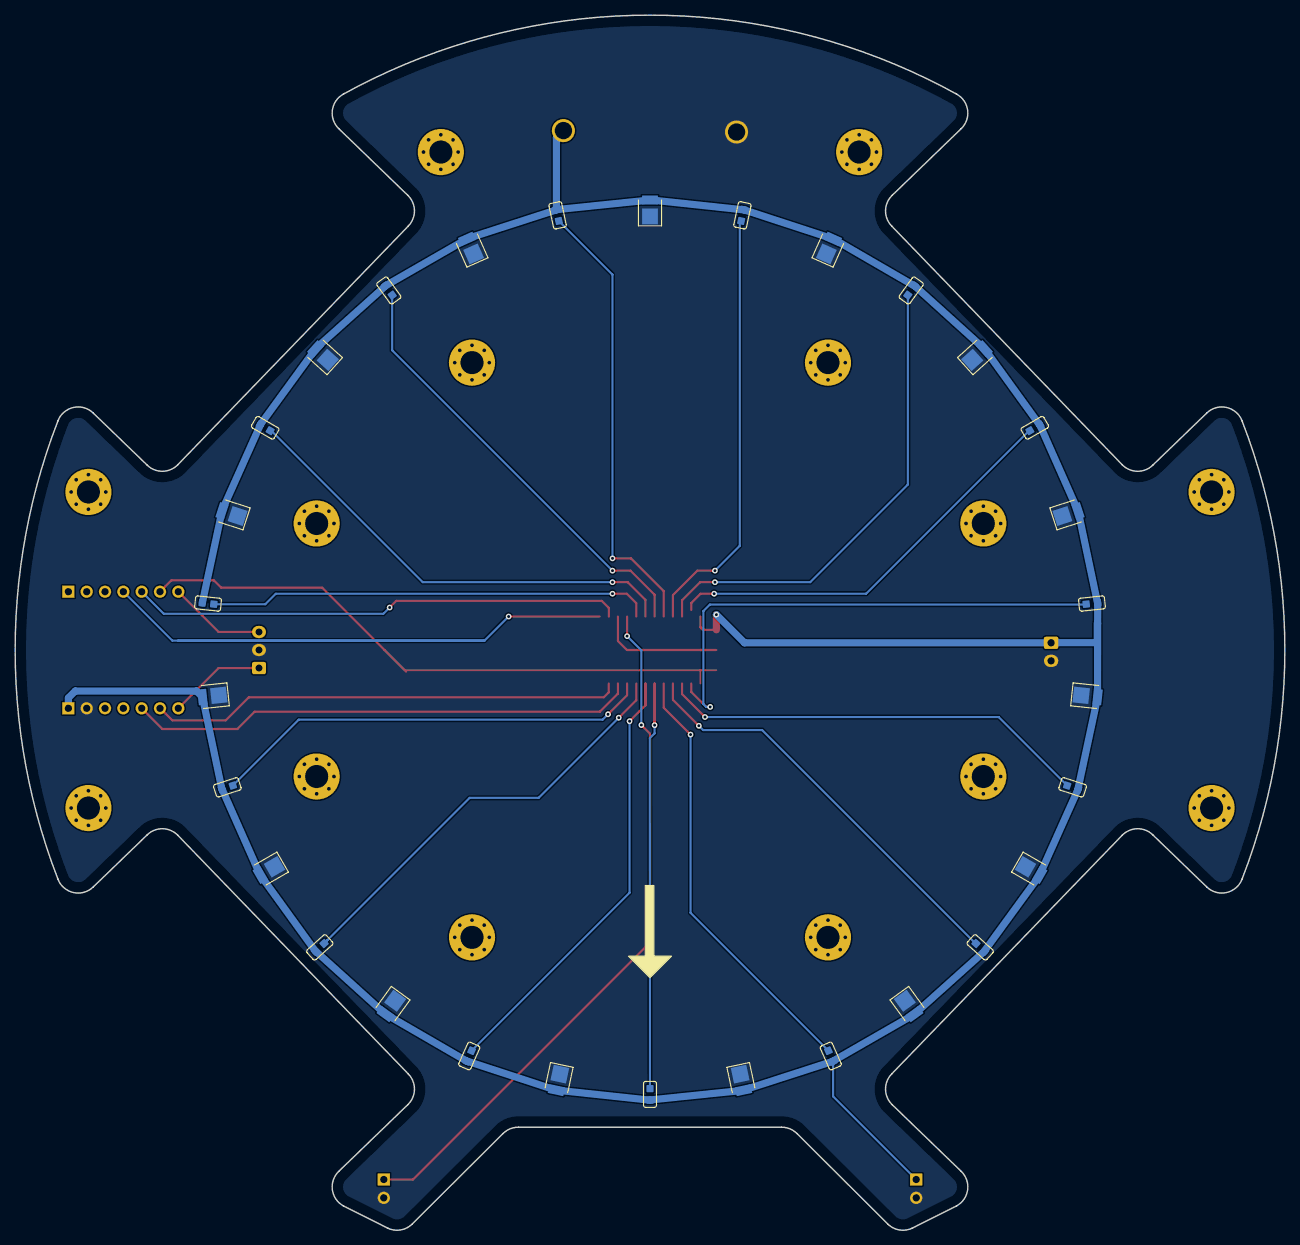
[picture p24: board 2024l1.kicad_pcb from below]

Board: 2 copper layers, 176.0 x 168.4 mm, 57 parts (30 on the bottom side), 26 nets.

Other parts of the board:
kibuzzard-655F61C6: G***; kibuzzard-655F61C6
kibuzzard-655F6265: G***; kibuzzard-655F6265

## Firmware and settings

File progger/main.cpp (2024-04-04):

#include <Arduino.h>
#include <Adafruit_BNO08x.h>
#include <Arduino.h>
#include <SPI.h>

//motor driver ports
int ena = 0;
int enb = 5;
int enc = 6;
int end = 12;

int in1 = 1; //driver 1 motor a
int in2 = 2;
int in3 = 3; //driver 1 motor b
int in4 = 4;

int in5 = 7; //driver 2 motor a
int in6 = 8;
int in7 = 9; //driver 2 motor b
int in8 = 10;

int switchpin = 18;

int ledPin = 13;

int buffer = 0;
int buildup = 0;

float ball_x = 0;
float ball_y =  0;
float ball_y_old = 0;

float wheel1 = 0;
float wheel2 = 0;
float wheel3 = 0;
float wheel4 = 0;


void motor(float motor1, float motor2, float motor3, float motor4) {

}



void setup() {
  // put your setup code here, to run once:
  pinMode(ena,OUTPUT);
  pinMode(enb,OUTPUT);
  pinMode(enc,OUTPUT);
  pinMode(end,OUTPUT);
  pinMode(in1,OUTPUT);
  pinMode(in2,OUTPUT);
  pinMode(in3,OUTPUT);
  pinMode(in4,OUTPUT);
  pinMode(in5,OUTPUT);
  pinMode(in6,OUTPUT);
  pinMode(in7,OUTPUT);
  pinMode(in8,OUTPUT);
  pinMode(ledPin, OUTPUT);
  pinMode(switchpin,INPUT);


  
  pinMode(20,INPUT);
  pinMode(21,INPUT);

  


  Serial.begin(512000);
  Serial5.begin(100000);
  // Serial.println("begin");
  // Serial5.begin(100000); //TX5, RX5 (to OpenMV)
  // //baudrate set at 100k to match with OpenMV

}

// void forward() {
  



// }



void loop() {

  if (analogRead(switchpin) > 800) {
    digitalWrite(ledPin,HIGH);
    uint8_t speed = 255;
    analogWrite(ena, speed);
    analogWrite(enb, speed);
    analogWrite(enc, speed);
    analogWrite(end,speed);
   

    if (Serial5.available()) {
      //a packet is 8 bits : ABBCCCCC - where A is a completeness marker, BB is a 2-bit identity_marker and CCCCC is the 5-bit payload.
      unsigned char incoming_pkt = Serial5.read();
      int completeness_marker = incoming_pkt >> 7;
      int identity_marker = (incoming_pkt % 128) >> 5; 
      int payload = (incoming_pkt % 32);

      buffer = buffer + (payload << buildup * 5);

      buildup = buildup + 1;

      if (completeness_marker == 1) { //ending packet
        wheel1 = 0;
        wheel2 = 0;
        wheel3 = 0;
        wheel4 = 0;
        ball_x = floor(buffer / 1000); //x
        ball_y = (buffer % 1000); //y
        
        float ball_y_offset =  (120 - ball_y) / 120;
        wheel1 = (wheel1 + ball_y_offset) * 2;
        wheel2 = (wheel2 - ball_y_offset) * 2;
        wheel3 = (wheel3 - ball_y_offset) * 2;
        wheel4 = (wheel4 + ball_y_offset) * 2;
        buffer = 0;
        buildup = 0;
      }
    }
    analogWrite(ena, int (abs(wheel1) * 200));
    analogWrite(enb, int (abs(wheel2) * 200));
    analogWrite(enc, int (abs(wheel3) * 200));
    analogWrite(end, int (abs(wheel4) * 200));

    if (wheel1 > 0) {digitalWrite(in1,HIGH); digitalWrite(in2,LOW);} else {digitalWrite(in2,HIGH); digitalWrite(in1,LOW);}
    if (wheel2 > 0) {digitalWrite(in3,HIGH); digitalWrite(in4,LOW);} else {digitalWrite(in4,HIGH); digitalWrite(in3,LOW);}
    if (wheel3 > 0) {digitalWrite(in5,HIGH); digitalWrite(in6,LOW);} else {digitalWrite(in6,HIGH); digitalWrite(in5,LOW);}
    if (wheel4 > 0) {digitalWrite(in7,HIGH); digitalWrite(in8,LOW);} else {digitalWrite(in8,HIGH); digitalWrite(in7,LOW);}

    Serial.println(wheel1);
    Serial.println(wheel2);
    Serial.println(wheel3);
    Serial.println(wheel4);
  }
  else {
    digitalWrite(ledPin,LOW);
    uint8_t speed = 0;
    analogWrite(ena, speed);
    analogWrite(enb, speed);
    analogWrite(enc, speed);
    analogWrite(end,speed);
  }
}

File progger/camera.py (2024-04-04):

import time
import math
import struct

import ulab
import image
import sensor
from pyb import UART, LED
from ulab import numpy as np


# --------------------------------------------- CONFIG ---------------------------------------------

DEBUG_CAMERA = True

# Camera system
# ----- OLDBOT -----
CAMERA_CENTER = np.array((159, 140))
CAMERA_ROI = (32, 14, 244, 227)
HMIRROR = True
VFLIP = False
TRANSPOSE = False
"""
0 6
10 10
20 17
30 24
40 40
50 51
60 58
70 65
80 68
90 72
100 76
110 79
120 83
130 84
140 90
150 92
160 95
170 99
180 100
190 101
200 102
"""
DISTANCE_COEFFICIENTS = np.array(
    [-3.49578147e-06, 1.03941994e-03, -8.13682248e-02, 3.22518576e00, -1.57496452e01],
    # [ 9.53340581e-05, -1.11504149e-02,  9.92479690e-01,  1.75040766e+00]
    # [2.45641451e-06, -4.13791515e-04, 2.54199085e-02, 1.71702709e-01, -7.67467924e-02]
)
# ----- NEWBOT -----
# CAMERA_CENTER = np.array((146, 157))
# CAMERA_ROI = (0, 0, 240, 320)
## CAMERA_CENTER = np.array((125, 177))
## CAMERA_ROI = (19, 76, 210, 210)
# HMIRROR = False
# VFLIP = False
# TRANSPOSE = True
# """
# 0 12
# 10 13
# 20 50
# 30 66
# 40 75
# 50 86
# 60 98
# 70 103
# 80 109
# 90 113
# 100 117
# 110 120
# 120 124
# 130 124
# 140 126
# 150 128
# 160 131
# 170 131
# 180 132
# 190 133
# 200 133
# """
# DISTANCE_COEFFICIENTS = np.array(
# [ 1.17041523e-09, -4.21577792e-07,  5.77787509e-05, -3.65929209e-03,
# 1.05876533e-01, -6.34293210e-01, -2.28222842e+00]
# )
# ------------------

# Camera configuration
GAIN = 20
# RGB_GAIN = (-6, -20, -20)
RGB_GAIN = (-7.0, -7.0, -1.0)
# print(sensor.get_gain_db())
# print(sensor.get_exposure_us() * 0.21)

# Blob tracking
# ----- Computer Lab 3 -----
# BLUE_THRESHOLDS = [(35, 50, -10, 30, -70, -40)]
# YELLOW_THRESHOLDS = [(50, 75, -30, 0, 40, 80)]
# --------- AI Lab ---------
# BLUE_THRESHOLDS = [(45, 65, -30, 5, -40, -10)]
# YELLOW_THRESHOLDS = [(45, 80, 0, 40, 40, 80)]
# ---------- Home ----------
# BLUE_THRESHOLDS = [(25, 60, -15, 25, -60, -20)]
# YELLOW_THRESHOLDS = [(50, 90, -20, 5, 40, 80)]
# ---------- 318 ----------
## oldbot
# BLUE_THRESHOLDS = [(18, 33, -128, 15, -128, -3)]
# YELLOW_THRESHOLDS = [(64, 100, -128, 127, 59, 127)]
# EXPOSURE = 20000
## newbot
# BLUE_THRESHOLDS = [(0, 100, -128, 127, -128, -17)]
# YELLOW_THRESHOLDS = [(58, 100, -44, 12, 52, 127)]
# EXPOSURE = 20000
# ---------- lw only practice field 1640 ----------
# BLUE_THRESHOLDS = [(0, 60, -128, 127, -128, -10)]
# YELLOW_THRESHOLDS = [(35, 100, -16, 127, 30, 127)]
# GAIN = 20
# EXPOSURE = 13000
# ---------- lw only practice field 1130/1230 ----------
# BLUE_THRESHOLDS = [(20, 35, -128, 127, -128, -8)]
# YELLOW_THRESHOLDS = [(41, 100, -16, 127, 13, 127)]
# GAIN = 20
# EXPOSURE = 5000
# ---------- match 1 1000 ----------
## oldbot
## newbot
# BLUE_THRESHOLDS = [(0, 60, -36, -5, -128, -10)]
# YELLOW_THRESHOLDS = [(63, 100, -13, 127, 33, 127)]
##GAIN = 20
# EXPOSURE = 13000
# ---------- match 4 ----------
## oldbot
## newbot
BLUE_THRESHOLDS = [(20, 54, -128, -3, -128, -11)]
YELLOW_THRESHOLDS = [(61, 100, -15, 127, 17, 127)]
# GAIN = 20
EXPOSURE = 8000
# ---------- sus field -------
# BLUE_THRESHOLDS = [(29, 53, -128, 6, -128, -16)]
# YELLOW_THRESHOLDS = [(50, 100, -21, 127, 33, 127)]
##GAIN = 20
# EXPOSURE = 9000
#
BLOB_MERGE = False
BLOB_STRIDE = 1
BLOB_PIXEL_THRESHOLD = 15
BLOB_AREA_THRESHOLD = 15
BLOB_MARGIN = 5

F = np.eye(6, dtype=np.float)
B = 0
H = np.array(
    [
        [1, 0, 0, 0, 0, 0],
        [0, 1, 0, 0, 0, 0],
        [0, 0, 0, 0, 1, 0],
        [0, 0, 0, 0, 0, 1],
    ],
    dtype=np.float,
)
# Q represents process noise
# larger values reduce response time, smaller values reduce noise
Q = np.array(
    [
        [1e-3, 0, 0, 0, 0, 0],
        [0, 1e-2, 0, 0, 0, 0],
        [0, 0, 1e-2, 0, 0, 0],
        [0, 0, 0, 1e-2, 0, 0],
        [0, 0, 0, 0, 1e-2, 0],
        [0, 0, 0, 0, 0, 1e-3],
    ],
    dtype=np.float,
)
# R represents measurement noise
# smaller values indicate greater measurement precision
R = np.array(
    [
        [1e-3, 0, 0, 0],
        [0, 1e-3, 0, 0],
        [0, 0, 1e-3, 0],
        [0, 0, 0, 1e-3],
    ],
    dtype=np.float,
)

# --------------------------------------------- SETUP ----------------------------------------------

LED(2).off()  # Turn off the green LED

sensor.reset()
sensor.set_pixformat(sensor.RGB565)
sensor.set_framesize(sensor.QVGA)
sensor.set_hmirror(HMIRROR)
sensor.set_vflip(VFLIP)
sensor.set_transpose(TRANSPOSE)
sensor.skip_frames(time=1000)

sensor.set_auto_gain(False, gain_db=GAIN)
sensor.set_auto_exposure(False, exposure_us=EXPOSURE)
sensor.set_auto_whitebal(
    False, rgb_gain_db=RGB_GAIN
)  # Must be turned off for blob tracking
sensor.set_brightness(0)
sensor.set_contrast(3)
sensor.set_saturation(3)
sensor.skip_frames(time=1000)

# while True:
# print(sensor.get_exposure_us())
# img = sensor.snapshot()

serial = UART(3, 1000000)

# -------------------------------------------- METHODS ---------------------------------------------


def pixels_to_cm(x):
    return np.polyval(DISTANCE_COEFFICIENTS, [x])[0]


def find_object(img, lab_threshold, draw_color):
    # Find blobs
    blobs = img.find_blobs(
        lab_threshold,
        merge=BLOB_MERGE,
        roi=CAMERA_ROI,
        x_stride=BLOB_STRIDE,
        y_stride=BLOB_STRIDE,
        pixels_threshold=BLOB_PIXEL_THRESHOLD,
        area_threshold=BLOB_AREA_THRESHOLD,
        margin=BLOB_MARGIN,
    )

    # Find the largest blob
    max_area = 0
    detected_blob = None
    for blob in blobs:
        if blob.area() > max_area:
            max_area = blob.area()
            detected_blob = blob

    if not detected_blob:
        return None

    # Find the base of the blob
    mal = detected_blob.minor_axis_line()
    base1 = np.array(mal[0:2])
    base2 = np.array(mal[2:4])
    base1 -= CAMERA_CENTER
    base2 -= CAMERA_CENTER
    base1_distance = math.sqrt(base1[0] ** 2 + base1[1] ** 2)
    base2_distance = math.sqrt(base2[0] ** 2 + base2[1] ** 2)
    position = base1 if base1_distance < base2_distance else base2
    distance = base1_distance if base1_distance < base2_distance else base2_distance

    # Annotate the blob if we're debugging
    if DEBUG_CAMERA:
        img.draw_ellipse(detected_blob.enclosed_ellipse(), color=draw_color)
        absolute_position = CAMERA_CENTER + position
        img.draw_cross(
            int(absolute_position[0]), int(absolute_position[1]), color=draw_color
        )

    # Find the relative polar coordinates of the object
    angle = (math.degrees(math.atan2(position[1], position[0])) + 90) % 360
    distance = pixels_to_cm(distance)

    return angle, distance
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

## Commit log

2023-07-07 brought files to new repo
    [l1.kicad_pcb, l1.kicad_sch]
2023-07-07 hamburger cheeseburger big mac whopper
    hamburger cheeseburger
    [l1.kicad_sch]
2023-07-19 co
    coaeoo
    [2023l3-int.kicad_sch, ir.kicad_sch, l1.kicad_sch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]
2023-07-19 L2 net labels
    [l2.kicad_sch]
2023-07-19 Revert "L2 net labels"
    This reverts commit 1f70947ea7bd54b8f040afb39f0aba0e0f35dfe9.
    [l2.kicad_sch]
2023-07-19 I like monkey balls.
    [l2.kicad_sch]
2023-07-25 activation circuit, motor drivers removed from l1
    [l1.kicad_pcb, l1.kicad_sch]
2023-07-26 Updated stuff
    [l1.kicad_pcb, l1.kicad_sch]
2023-12-10 v1.0 of L1 (sent to production), schematic for L2
    [0603Inductor.step, 1040 inductor v1.step, 1040Inductor.step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]
2024-01-12 producion l1, fucked l2 need to redo, todo: l2,l3
    [0603Inductor.step, 1040Inductor.step, 2023l3-int.kicad_sch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]
2024-02-28 2024-02-28 production
    [bom.csv, designators.csv, l2.kicad_pcb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]
2024-02-28 file organisation
    [2023l3-int.kicad_sch, ir.kicad_sch]

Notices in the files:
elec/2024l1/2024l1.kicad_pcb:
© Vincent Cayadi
